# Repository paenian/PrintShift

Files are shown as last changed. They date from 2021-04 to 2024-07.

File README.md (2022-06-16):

# Prusa Mini Conveyor Belt!

Status: Fully Functional!

Quick overview - this repo contains all the files I used to add a conveyor belt to my Prusa Mini.

The latest version fits a Prusa Mini, and lives here: https://github.com/paenian/PrintShift/tree/main/prusa%20mini/printshift%204.0%20ejector

## BELT MATERIAL
The current belt is made from .2mm thick Kapton, ordered from AliExpress and lasercut.  You can totally hand-cut it, but tracking of the belt is a bit of a pain.

The belt is designed to be easily replaced - other materials I have used:
 * .01" polyester film: Cuts easily, prints stick very well with hairspray.  This belt has higher thermal expansion, but with PLA or lower temps on the heater it works great, and is quite cheap.  It does break down at PETG temperatures, so I recommend the kapton as the most versatile belt.
   * https://www.mcmaster.com/8567K92/
   * Use hairspray to help prints stick.
 * .225mm Kapton: Low thermal expansion.  More expensive than the polyester.
   * https://www.aliexpress.com/item/4000699107361.html?spm=a2g0s.9042311.0.0.19534c4dqCLd9z
   * Use hairspray to help prints stick.
 * .005" ULTEM/PEI film: Prints stick well, but it's too flexible.  After ~10 hours printing, sheet sheared while printing.  It was under a lot of tension.  Gets expensive quick.
   * https://catalog.cshyde.com/item/films/ultem-pei-polyethermide-resin/36-5f
 * .01" ULTEM/PEI film: Same story as the .005; less flexible, of course, so prints warped less on it.  However, it did shear mid-print after maybe 100 hours of printing - it lasted longer, but split right in two.  My assumption is more due to fatigue from all the rolling.
   * https://catalog.cshyde.com/item/films/ultem-pei-polyethermide-resin/36-10f

 I have used thicker and stiffer belts, too - various stainless steels and conveyor materials, usually covering the belt itself in PET tape to get good adhesion and release.  However, these require larger, stronger rollers - so aren't compatible with the printers in this repository.

## CONTROL
The belt is controlled by a microswitch mounted on the top of the Z axis.  When the Z gets high enough and Y is forward enough, your parts scoot.  The nice part is no modification of the firmware is required - just some special start and end GCODE in your slicer.  I do take power for the motor from inside the Prusa Mini box for neatness - I like my printers as self-contained as possible.

The other modifications to the Prusa Mini involve raising the bed 4mm - so combined with the switch up top, you're losing about 15mm of usable Z axis.

Right now, the belt is 145mm in width - so your Y axis shrinks a bit when printing on the belt.  You can, however, still print using the entire bed - just put the metal build plate on top of the belt!

## INSTALLATION
The projects in this repository are best described on YouTube: https://www.youtube.com/paulchase

Instructions, videos, tips and tricks will all be posted there.

This project is supported by patrons on Patreon - go to https://www.patreon.com/PrintShift if you'd like to help develop part ejecting printers!

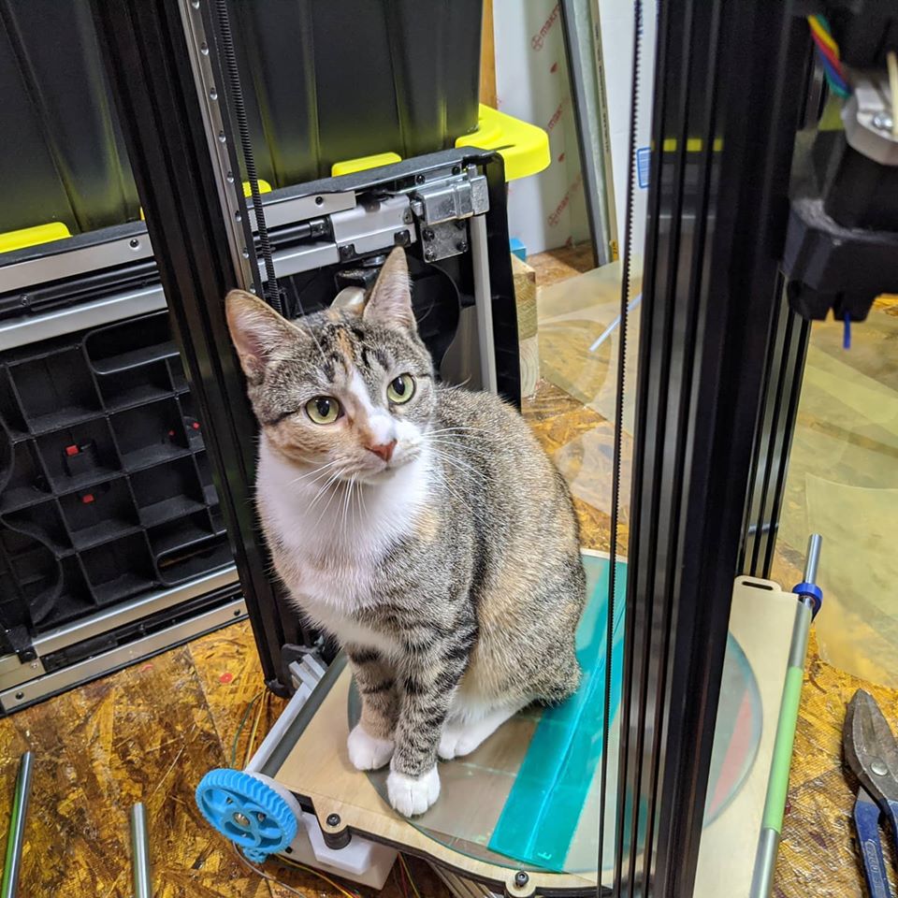
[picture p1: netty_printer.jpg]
Netty is the official mascot


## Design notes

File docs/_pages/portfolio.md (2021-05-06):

---
title: PrintShift Guides
layout: collection
permalink: /portfolio/
collection: portfolio
entries_layout: grid
classes: wide
---

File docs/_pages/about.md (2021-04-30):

---
permalink: /about/
title: "About"
---

The PrintShift Project is adding conveyor belts to conventional 3D printers.  The project began by adding part ejection to Prusa Minis, which is now feature-complete and has been running for thousands of printing hours.

The project will continue to work on belts, part ejection and related technologies, as well as working to improve the Prusa Mini's ejector.

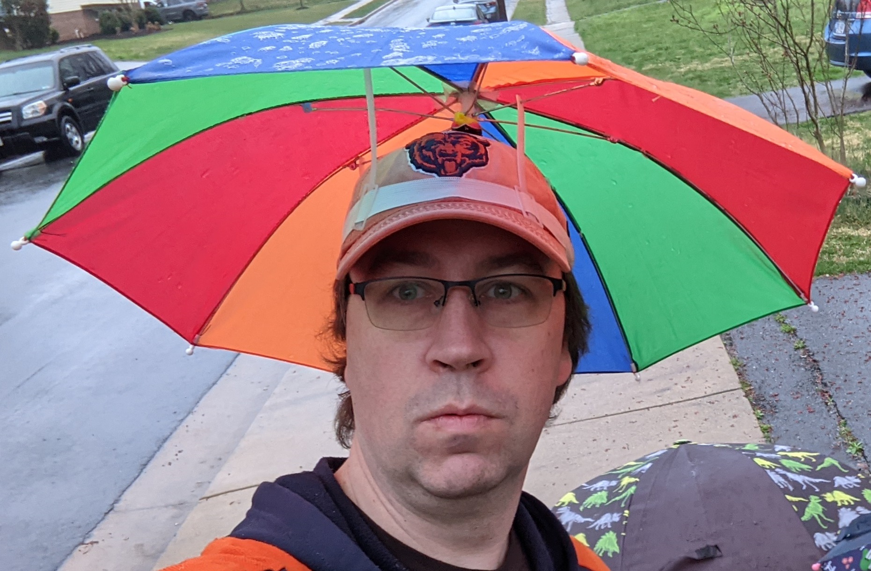
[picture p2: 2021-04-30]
docs/assets/images/bio-photo.jpg

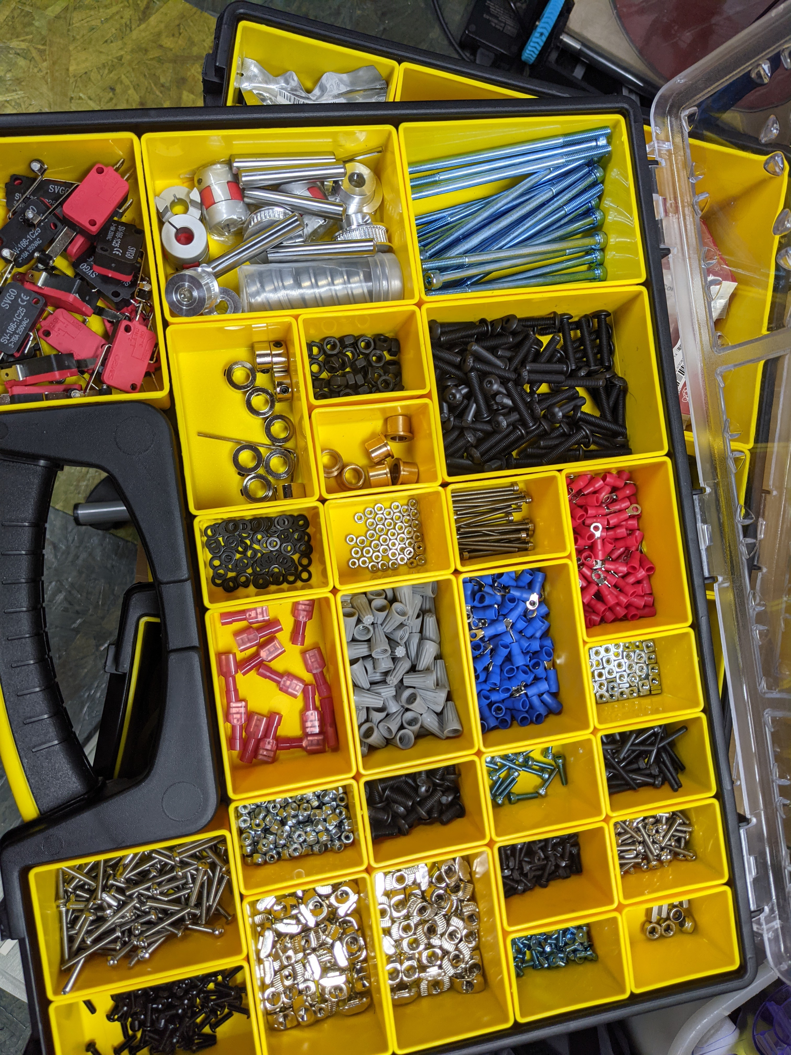
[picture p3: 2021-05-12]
docs/assets/images/BoM-photo.jpg

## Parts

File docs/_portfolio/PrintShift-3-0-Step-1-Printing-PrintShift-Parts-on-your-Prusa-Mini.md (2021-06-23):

---
title: "PrintShift 3.0 Step 1: Printing PrintShift Parts on your Prusa Mini"
---

# PrintShift 3.0 Build Series: Step 1

This page details how to print the PrintShift parts.  I like to print the parts on the Prusa Mini that's destined to be PrintShift-ed - that way you know the machine is up and running and ready to go.  If your mini's acting up or failing in any way... repair it before you upgrade it!

## Materials Needed
1. Prusa Mini.  Yeah.  The whole thing.
   * Prusa sells 'em mostly built: [Prusa Mini+](https://shop.prusa3d.com/en/3d-printers/994-original-prusa-mini.html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)
   * Or barely assembled: [Prusa Mini+ Kit](https://shop.prusa3d.com/en/3d-printers/1387-original-prusa-mini-kit.html)
   * The mostly built goes together in under an hour; kit is maybe ten hours of building.
2. Filament!
   * You need some high-temperature filament like ABS, PETG, ASA or better for the bed-touching components.
   * You need some stiff filament for the Motor Mount and Standoff - PLA is fine, pretty much anything except TPU.

## Tools Needed
1. The Prusa Mini includes all the tools that you'll need for this portion of the build :-)
   * I do generally use my own 2.5mm allen wrench
   * And some side cutters to trim the zip tie

## Procedure
1. Build your Prusa Mini!  Just follow Prusa's instructions
  * Mostly Built:  [Prusa Mini+ Build Instructions](https://help.prusa3d.com/en/guide/building-your-mini_177717)
  * Kit: [Prusa Mini+ KIT Build Instructions](https://help.prusa3d.com/en/category/original-prusa-mini-kit-assembly_1215)
2. Test Print!  Prusa includes a few on the USB stick that comes with the printer.
3. Print Large PrintShift Parts
  * These are printed with .25mm layers, 3 perimeters, 50% cubic infill.  They need to be strong and rigid.
  * [Rear Motor Plate](https://github.com/paenian/PrintShift/blob/main/prusa%20mini/printshift%203.0%20ejector/rear%20motor%20plate.stl)
  * [Motor Plate Standoff with Pi](https://github.com/paenian/PrintShift/blob/main/prusa%20mini/printshift%203.0%20ejector/motor%20plate%20standoff%20-%20with%20pi.stl)

4. Print PrintShift - all small parts
  * This is all of the other parts; they need to handle the higher temperatures of the bed, so must be ABS, ASA, PETG or similar. 
  * Mine are printed in blue ABS, .25mm layers, 3 perimeters, 50% cubic infill.  They need to be strong, rigid, and stable up to 100C.
  * [Small Parts](https://github.com/paenian/PrintShift/blob/main/prusa%20mini/printshift%203.0%20ejector/PrintShift%20-%20all%20small%20parts.stl)
5. Print (optional) Raspberry Pi components
  * [pi 4 case top](https://github.com/paenian/PrintShift/blob/main/prusa%20mini/mini%20mounts%20and%20enhancements/raspi/Pi_4_Case_40mm_fan_top%20v3.stl)
  * [pi 4 case bottom](https://github.com/paenian/PrintShift/blob/main/prusa%20mini/mini%20mounts%20and%20enhancements/raspi/Pi_4_Case_bottom%20v3.stl)
  * [pi 3 case top](https://github.com/paenian/PrintShift/blob/main/prusa%20mini/mini%20mounts%20and%20enhancements/raspi/pi_3_case_top.stl)
  * [pi 3 case bottom](https://github.com/paenian/PrintShift/blob/main/prusa%20mini/mini%20mounts%20and%20enhancements/raspi/pi_3_case_bottom.stl)
  * [Rear camera mount](https://github.com/paenian/PrintShift/blob/main/prusa%20mini/mini%20mounts%20and%20enhancements/raspi/rear%20camera%20mount.stl)
6. Gather the rest of the parts from the [Bill of Materials](/portfolio/Bill-of-Materials/) and start [Building the Belt](/portfolio/PrintShift-3-0-Step-2-Belted-Bed-Build)!

## Video Walkthrough
{% include video id="aPgevA5sr5U" provider="youtube" %}

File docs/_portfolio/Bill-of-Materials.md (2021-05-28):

---
title: "PrintShift Bill of Materials"
excerpt: "Shortcut to the Google Docs active BOM, with some discussion on parts."
header:
  image: /assets/images/BoM-photo.jpg
  teaser: assets/images/BoM-photo.jpg
---
# PrintShift Bill of Materials

The LIVE Bill of Materials will live here:

[BoM on Google Sheets](https://docs.google.com/spreadsheets/d/1gTF6RvdNjgoJNNBqXj-OhuOjt69_Wzujfkq8HkN1fU4/edit?usp=sharing)
Anyone can comment on the google doc - ideally, comments will be resolved and then removed.

[CSV Snapshot as of 5/11/2021](/assets/PrintShift BOM - Sheet1.csv)

## BoM Sections
The BoM is divided into sections based on where the parts are used; this is to try to help organize it, and to more easily edit and update.  

### Conveyor Belt Hardware
There is a separate page to cover and discuss [belt materials](/portfolio/Belt Materials/)

The rest of the parts here are hardware for mounting the belt to the Prusa Mini's bed carriage.  The conveyor belt hardware can be added at any point, and while it raises the bed 4mm it does not affect normal operation of the mini in any way... at least until you slide a belt onto it :-)

Basically none of these parts can be substituted out without redesigning something, but there are bound to be cheaper suppliers, especially in quantity.

### Ejector Hardware
These parts are everything required to mount and run the ejector motor, as well as connect it to the conveyor belt mounted on the bed.
This includes the control microswitch and wiring.

Generally, installing these I would include the 5v buck converter to run a raspberry pi - although using wire nuts to attach means it's easy to add later.

A lot of these parts (wire nuts, crimp lugs, getting power for the motor in the first place) could be substituted out as desired; I chose them as the easiest to install reliably.

### Belt Material
The Kapton and various tapes used for the belt.  I treat tapes as '1 roll per printer' so they add a little more to the BoM than I would like... but it's better to be expansive I think.

### Raspberry Pi
Mounting a Raspberry Pi and running Octoprint on the mini is optional, but adds a huge amount of functionality.  In the future, Prusa has said that they would expand the capabilities of the BuddyBoard and its ethernet port, so perhaps the pi will become redundant... but I don't think that it will.

The Raspberry Pi + camera allows you to access your printer from far away to monitor and start or queue prints.  Additionally, I use Octoprint plugins to connect my machines to the cloud and add print queueing.

### Optional Parts
This includes parts trays, GoPro mounts, my silly clock mount (I love it), and the base to put the printer on if you utilize a rackmount or other print farm system.

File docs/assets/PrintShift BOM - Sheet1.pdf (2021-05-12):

# of PrintShifts to build | 10 Part | Type | Notes | Quantity Needed Per-Machine Price | Pack Quantity | Pack Price | Price Per Part | Packs Needed | extra part quantityPurchase Price | Purchase Link Conveyor Belt Hardware Shaft collar | 8mm | For front of drive roller | 1 | $0.90 | 10 | $8.99 | $0.90 | 1 | 0 | $8.99 | https://smile.amazon.com/gp/product/B07V41FRZS/ref=ppx_yo_dt_b_asin_title_o00_s01?ie=UTF8&psc=1

8mm shaft, 210mm | hardened steel | drive roller - cut into 183mm for the idler, remainder works great for the drive roller 1 | $7.20 | 2 | $14.39 | $7.20 | 5 | 0 | $71.95 | https://smile.amazon.com/Linear-Motion-FEYRINX-Hardened-Printer/dp/B085DQYQYH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
8mm shaft, 183mm | hardened steel | idler - cut down from the 400mm above | 0 | $0.00 | 2 | $14.39 | $7.20 | 0 | 0 | $0.00
flanged bushings | 8mm | drive roller guides | 2 | $6.88 | 1 | $3.44 | $3.44 | 20 | 0 | $68.80 | https://www.mcmaster.com/5448T2/ M3 Hex Standoffs, 10mm long 4.5 or 5mm hex | lift the bed up | 6 | $6.30 | 1 | $1.05 | $1.05 | 60 | 0 | $63.00 | https://www.mcmaster.com/94868A166/ M3 screw, 8mm | flat head | replace the bed screws - easier to deal with9 | $1.64 | 50 | $9.10 | $0.18 | 2 | 10 | $18.20 | https://www.mcmaster.com/91304A101/ M5 screws, 25mm | button head | tension the idler | 2 | $0.31 | 50 | $7.86 | $0.16 | 1 | 30 | $7.86 | https://www.mcmaster.com/91306A669/ M5 nuts | hex | tension the idler | 2 | $0.04 | 100 | $1.76 | $0.02 | 1 | 80 | $1.76 | https://www.mcmaster.com/90592A095/
Ejector Hardware F608ZZ flanged ball bearings | 8x22x7 | 2 | $2.74 | 10 | $13.69 | $1.37 | 2 | 0 | $27.38 | https://smile.amazon.com/gp/product/B07N62N7N2/ref=ppx_yo_dt_b_asin_title_o00_s00?ie=UTF8&psc=1
flexible shaft coupling | 8mm to 8mm | Link the belt and the motor | 1 | $6.50 | 2 | $12.99 | $6.50 | 5 | 0 | $64.95 | https://smile.amazon.com/gp/product/B08QVKMDC6/ref=ppx_yo_dt_b_asin_title_o00_s01?ie=UTF8&psc=1
40T GT2 pulley | 8mm bore | Attach to belt | 1 | $4.00 | 2 | $7.99 | $4.00 | 5 | 0 | $39.95 | https://smile.amazon.com/gp/product/B07K6BRL4K/ref=ppx_yo_dt_b_asin_title_o00_s01?ie=UTF8&psc=1
20T GT2 pulley | 6mm bore | Attach to motor | 1 | $1.60 | 5 | $7.99 | $1.60 | 2 | 0 | $15.98 | https://smile.amazon.com/gp/product/B08P6KY773/ref=ppx_yo_dt_b_asin_title_o08_s00?ie=UTF8&psc=1 GT2 continuous belt | 79 teeth | connect the pulleys | 1 | $1.19 | 10 | $11.88 | $1.19 | 1 | 0 | $11.88 | https://smile.amazon.com/gp/product/B014QKEH26/ref=ppx_yo_dt_b_asin_title_o07_s00?ie=UTF8&psc=1
24v motor | 20RPM | ejector motor | 1 | $13.99 | 1 | $13.99 | $13.99 | 10 | 0 | $139.90 | https://smile.amazon.com/gp/product/B08FBBXZ67/ref=ppx_yo_dt_b_search_asin_title?ie=UTF8&psc=1
8mm dowel pin | 40mm long | ejector drive shaft | 1 | $0.96 | 10 | $9.60 | $0.96 | 1 | 0 | $9.60 | https://www.mcmaster.com/91595A573/ M3 screws, 12mm | socket head | Mount the motor | 2 | $0.10 | 100 | $5.19 | $0.05 | 1 | 80 | $5.19 | https://www.mcmaster.com/91292A114/ M5 screws, 100mm | socket head | Rear standoff for the motor assembly | 2 | $1.53 | 10 | $7.66 | $0.77 | 2 | 0 | $15.32 | https://www.mcmaster.com/91502A159/ M3 screws, 30mm | socket head | mount the switch | 2 | $0.42 | 50 | $10.51 | $0.21 | 1 | 30 | $10.51 | https://www.mcmaster.com/91290A130/ 3030 T-Nuts, M3 | post-assembly | mount the switch | 2 | $0.46 | 50 | $11.57 | $0.23 | 1 | 30 | $11.57 | https://smile.amazon.com/gp/product/B07GVJFZV8/ref=ppx_yo_dt_b_search_asin_title?ie=UTF8&psc=1 SV-166-1C25 microswitch | long hinge roller | ejector activator | 1 | $0.55 | 20 | $10.99 | $0.55 | 1 | 10 | $10.99 | https://smile.amazon.com/SV-166-1C25-Industrial-Switches-Terminals-Momentary/dp/B087PLT9MD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 Ring Terminal | M3, 22-16AWG wirepower the ejector | 1 | $0.07 | 150 | $9.99 | $0.07 | 1 | 140 | $9.99 | https://smile.amazon.com/smseace-Insulated-Electrical-Connectors-Assortment/dp/B08B5VS8ZR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 Spade connectors | 22-16AWG | wire in the switch | 2 | $0.50 | 80 | $19.98 | $0.25 | 1 | 60 | $19.98 | https://smile.amazon.com/gp/product/B07GP96LSS/ref=ppx_yo_dt_b_search_asin_image?ie=UTF8&psc=1 Wire Nuts | gray, 2*22awg terminals wire up the switch | 2 | $0.04 | 1000 | $17.99 | $0.02 | 1 | 980 | $17.99 | https://smile.amazon.com/Maxxima-Electrical-Connector-Screw-Terminal/dp/B07ZP8K8GJ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
22awg wire | Need about 2 meters total wire it all up | 0.5 | $1.41 | 6 | $16.95 | $2.83 | 1 | 1 | $16.95 | https://smile.amazon.com/gp/product/B07T4SYVYG/ref=ppx_yo_dt_b_search_asin_title?ie=UTF8&psc=1

Belt Material
.225mm Polyamide Film (Kapton).225x520x1m | The belt is 155mm wide by 430mm long - so cut 155mm strips, then trim down. | You can get 6 belts per mm, but quantity here is 2 - you always want a spare belt handy. 2 | $8.14 | 6 | $24.41 | $4.07 | 4 | 4 | $97.64 | https://www.aliexpress.com/item/4000473438004.html?spm=a2g0s.9042311.0.0.41374c4dFBWN0U
Powdercoating Tape | polyester film + silicone adhesive, .001" thick, 2" wide | 1 | $11.98 | 1 | $11.98 | $11.98 | 10 | 0 | $119.80 | https://www.mcmaster.com/7630A796/ Kapton Tape | 2" wide, Polyimide film + silicone adhesive, .0025" thick | 1 | $15.97 | 1 | $15.97 | $15.97 | 10 | 0 | $159.70 | https://smile.amazon.com/Heat-Resistant-Tape-Sublimation-Temperature/dp/B07KXXT1Y9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 Painter's Tape | 2" wide | 1 | $4.79 | 6 | $28.75 | $4.79 | 2 | 2 | $57.50 | https://smile.amazon.com/ScotchBlue-2090-48A-CP-Painters-Polypropylene-Backing/dp/B000A3DQGW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
Raspberry Pi Parts Buck Converter Module | USB-C | power the Raspberry Pi | 1 | $14.99 | 1 | $14.99 | $14.99 | 10 | 0 | $149.90 | https://smile.amazon.com/gp/product/B07ZQB6S3L/ref=ppx_yo_dt_b_asin_title_o05_s00?ie=UTF8&psc=1 USB->MicroUSB cable | 1ft | connect pi to the prusa mini | 1 | $7.99 | 1 | $7.99 | $7.99 | 10 | 0 | $79.90 | https://smile.amazon.com/gp/product/B07PFZDQP6/ref=ppx_yo_dt_b_asin_title_o05_s00?ie=UTF8&psc=1 Pi Camera Cable | 30cm | connect up pi camera | 1 | $1.33 | 6 | $7.99 | $1.33 | 2 | 2 | $15.98 | https://smile.amazon.com/gp/product/B08WLQBB93/ref=ppx_yo_dt_b_asin_title_o04_s00?ie=UTF8&th=1 Arducam | cheaper Pi Camera | 1 | $9.99 | 1 | $9.99 | $9.99 | 10 | 0 | $99.90 | https://smile.amazon.com/gp/product/B012V1HEP4/ref=ppx_yo_dt_b_asin_title_o04_s00?ie=UTF8&psc=1 Raspberry Pi 4 | 2GB | No need for more ram, but I think the faster processor is worth it over the older Pis. 1 | $34.99 | 1 | $34.99 | $34.99 | 10 | 0 | $349.90 | https://www.microcenter.com/product/621439/raspberry-pi-4-model-b-2gb-ddr4
2.5mm screws, 35mm long | socket head | 3 | $1.44 | 25 | $12.03 | $0.48 | 2 | 20 | $24.06 | https://www.mcmaster.com/91292A313/ 2.5mm nuts | hex | 3 | $0.22 | 50 | $3.69 | $0.07 | 1 | 20 | $3.69 | https://www.mcmaster.com/94150A310/
Optional Parts Collection Tray | 1 | $2.66 | 3 | $7.99 | $2.66 | 4 | 2 | $31.96 | https://smile.amazon.com/gp/product/B086X2YM9Q/ref=ppx_yo_dt_b_asin_title_o05_s01?ie=UTF8&psc=1
TOTAL PRICE | Per Machine, perfect: | $173.81 | $1,858.62 Per Machine, in quantity: | $185.86 Total for | 10 | $1,858.62
Price without Pi or Optional Parts | Per Machine, perfect: | $100.19 Per Machine, in quantity: | $110.33 Total for | 10 | $1,103.33

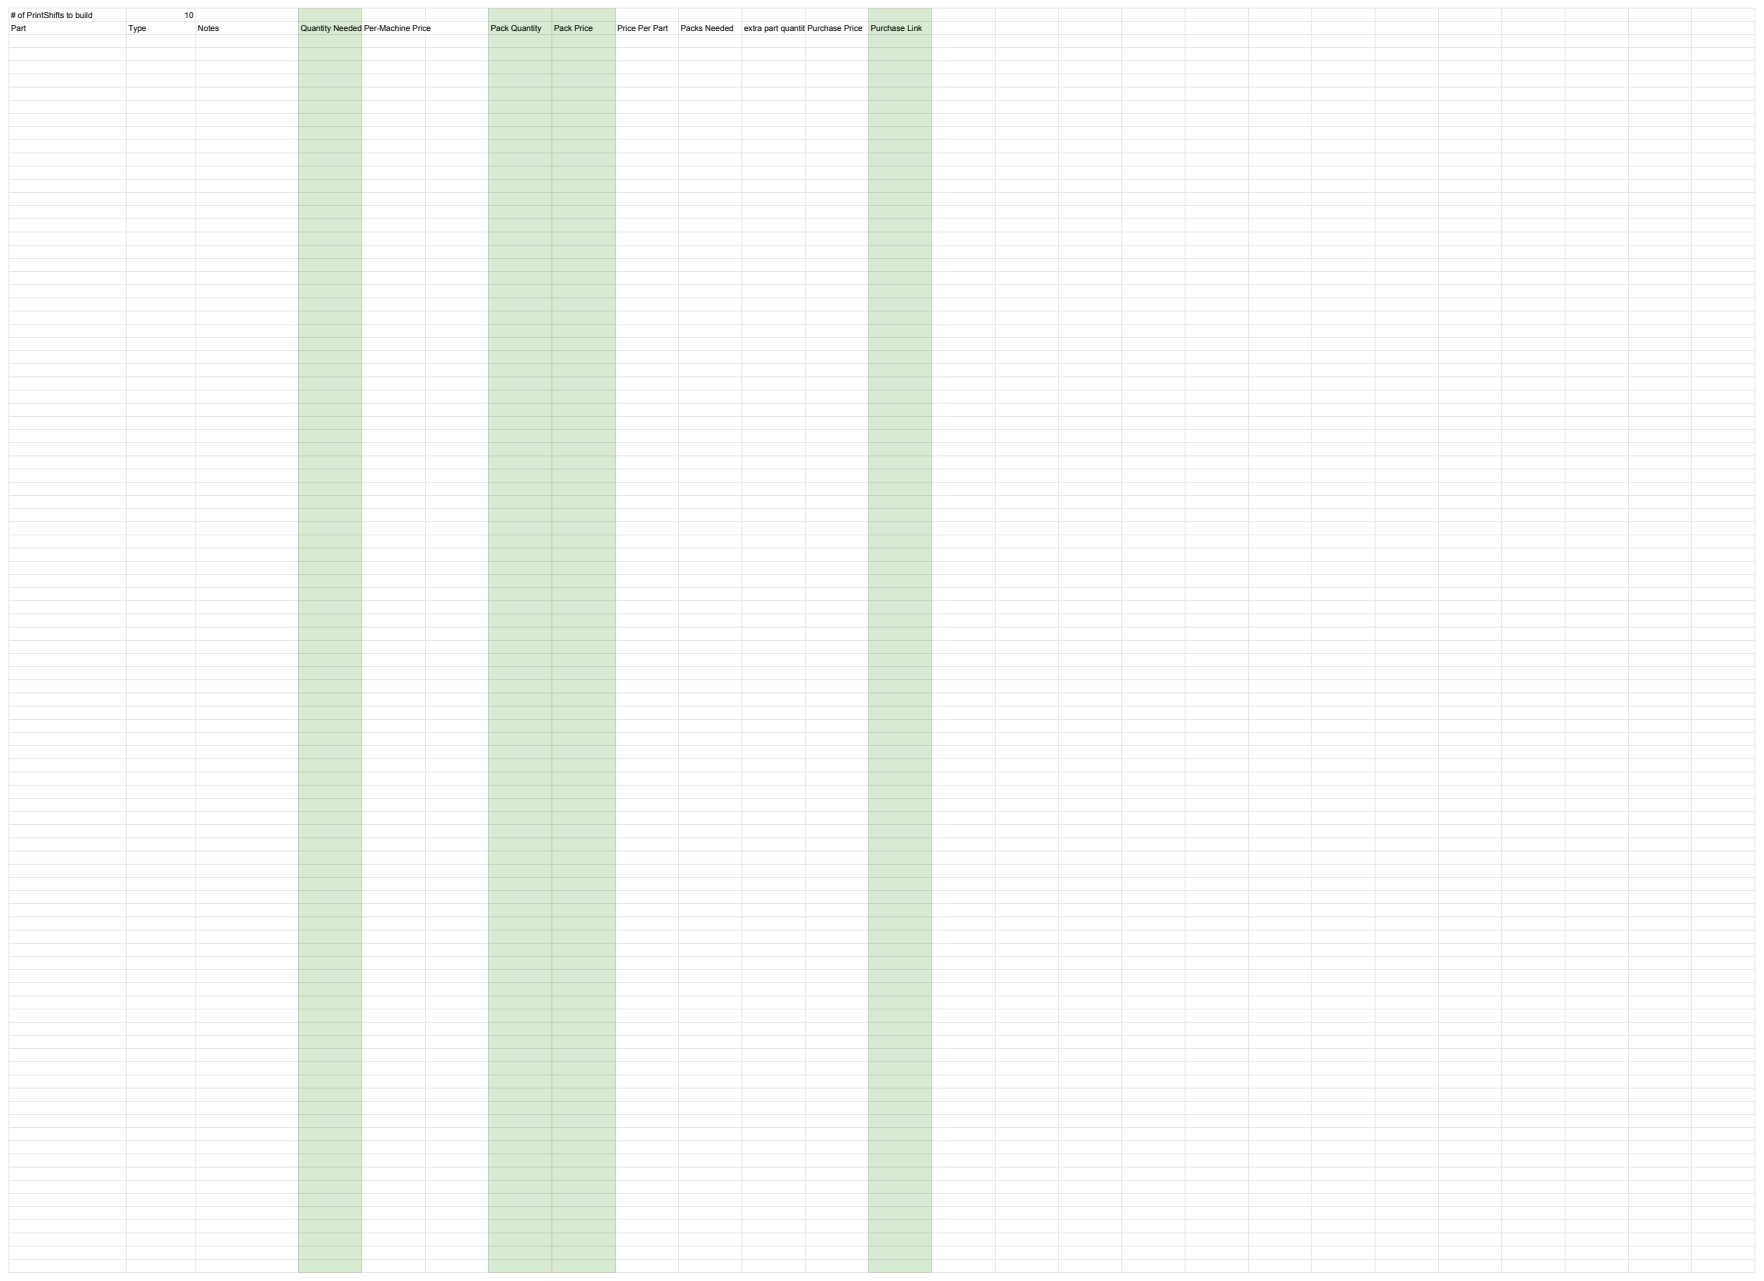
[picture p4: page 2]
# of PrintShifts to build; 10 Part; Type; Notes; Quantity Needed Per-Machine Price; Pack Quantity; Pack Price; Price Per Part; Packs Needed; extra part quantityPurchase Price; Purchase Link

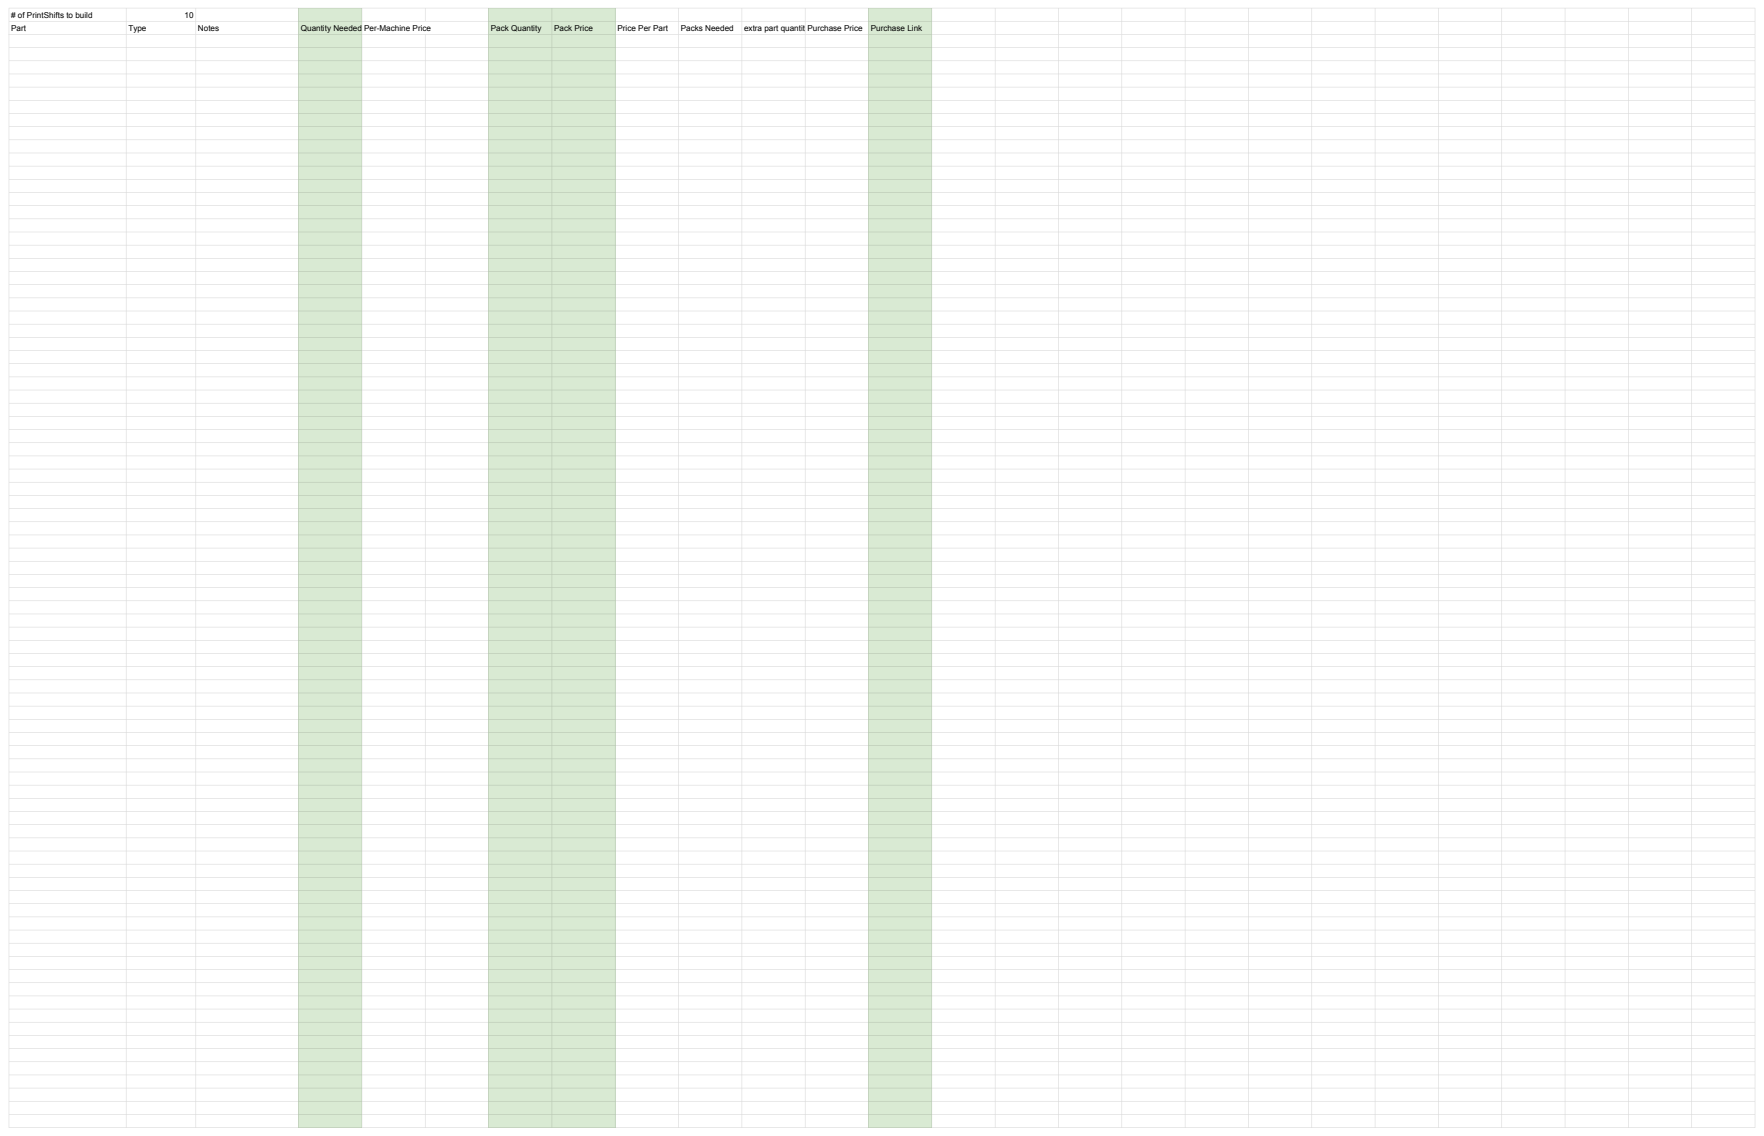
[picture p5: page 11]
# of PrintShifts to build; 10 Part; Type; Notes; Quantity Needed Per-Machine Price; Pack Quantity; Pack Price; Price Per Part; Packs Needed; extra part quantityPurchase Price; Purchase Link

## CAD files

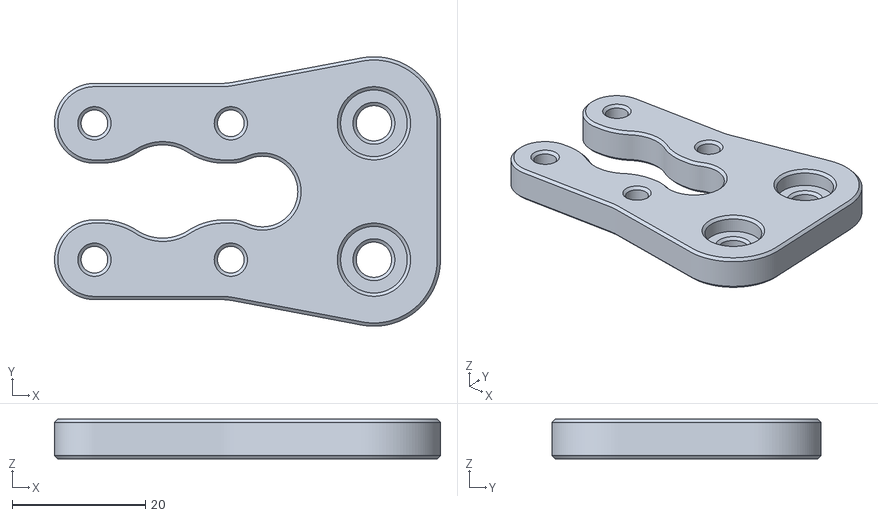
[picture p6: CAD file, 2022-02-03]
large bed ejector/doppelbot mounts/smooth rod mount.stl
58.0 x 40.5 x 6.00

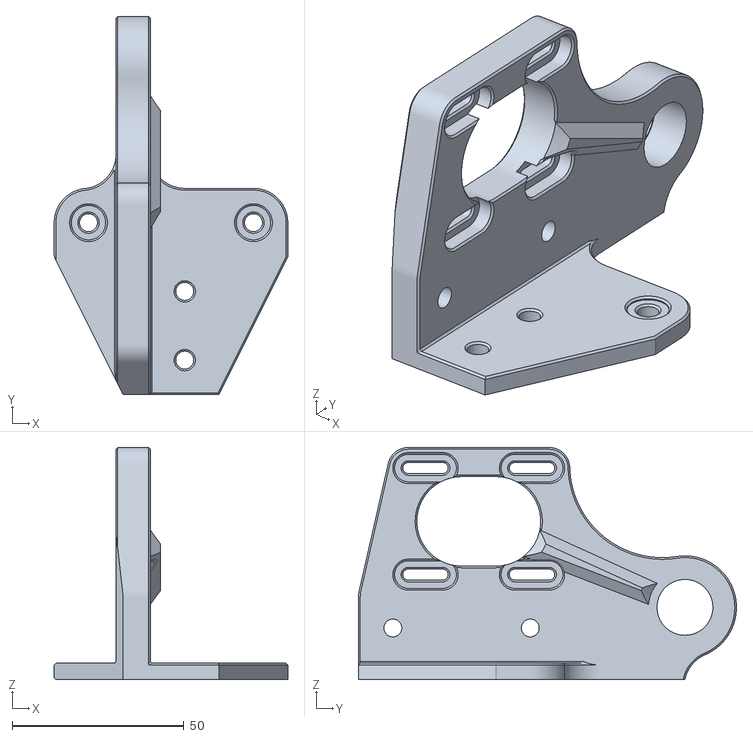
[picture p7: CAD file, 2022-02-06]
large bed ejector/motor and drive roller mount.stl
68.0 x 110.0 x 67.5

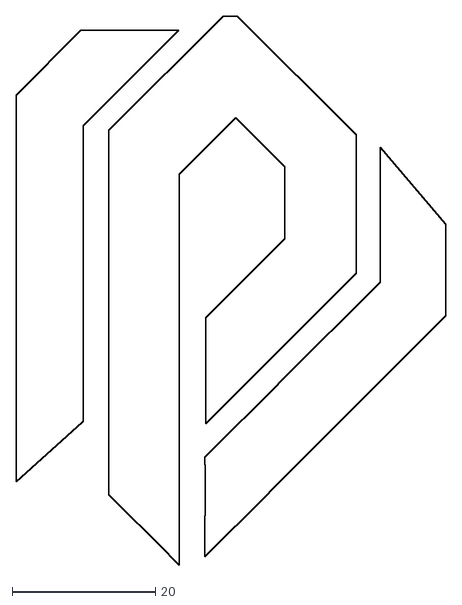
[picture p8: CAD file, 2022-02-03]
PrintShift logos/printshift_logo.dxf
60.0 x 76.6

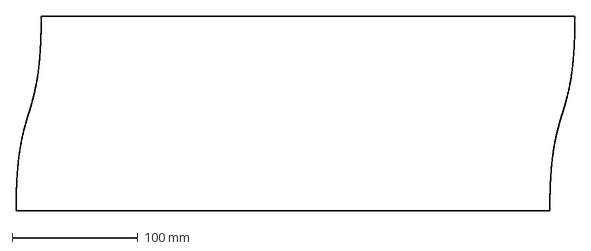
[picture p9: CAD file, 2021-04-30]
prusa mini/bed lasercutting/flat_angle-425x155.dxf
445.0 x 155.0 mm

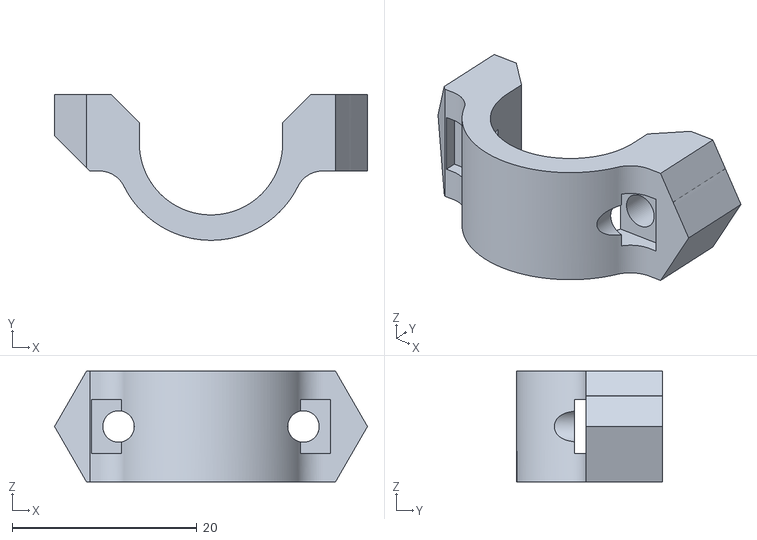
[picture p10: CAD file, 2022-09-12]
prusa mini/mini mounts and enhancements/prusa mini lm8uu clamp.stl
33.9 x 15.8 x 12.0

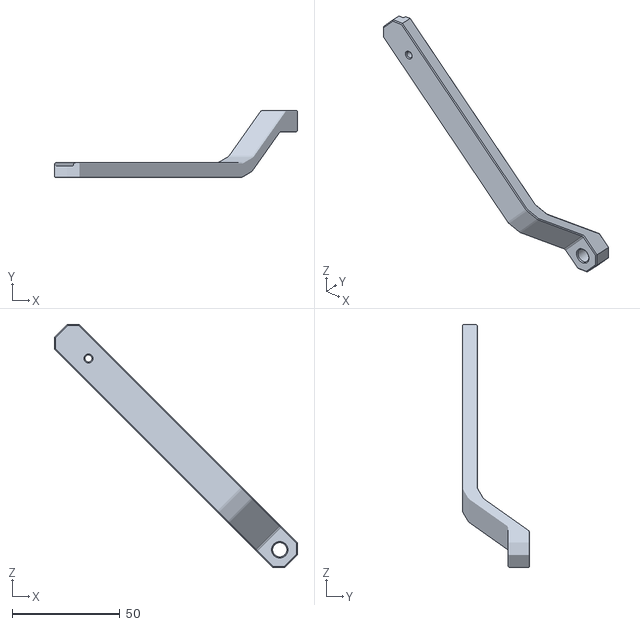
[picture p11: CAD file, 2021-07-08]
prusa mini/mini mounts and enhancements/raspi/corner webcam mount.stl
112.8 x 31.2 x 112.8

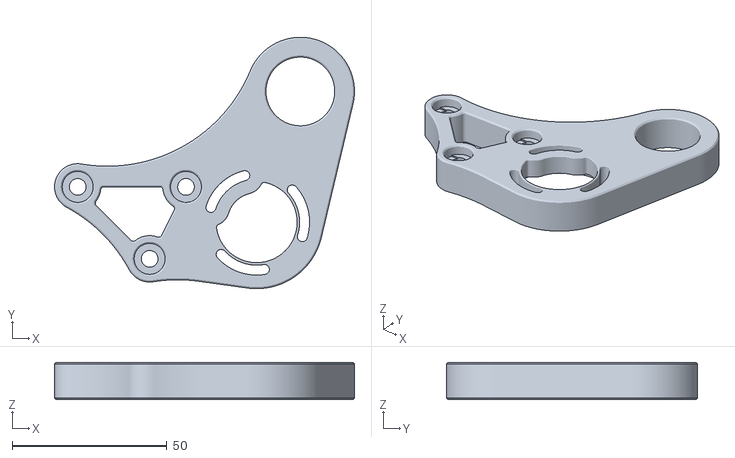
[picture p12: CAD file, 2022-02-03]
prusa mini/printshift 3.0 ejector/rear motor plate updated.stl
96.9 x 81.2 x 12.0

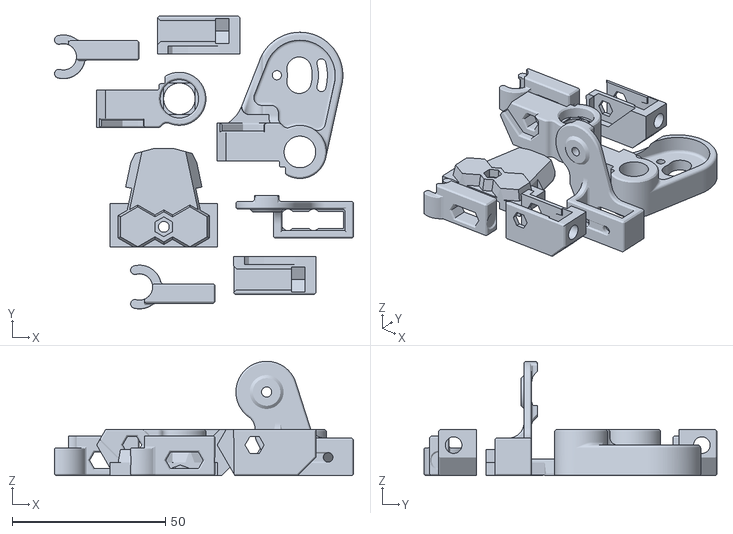
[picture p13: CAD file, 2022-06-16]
prusa mini/printshift 4.0 ejector/all parts arranged.stl
97.4 x 95.4 x 37.3

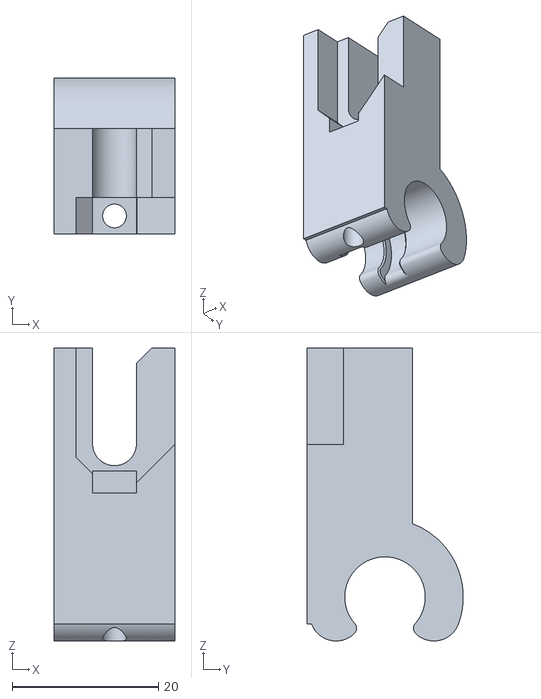
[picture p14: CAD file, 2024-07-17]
prusa mini/printshift 5.0 ejector/tensioner rod mount right.stl
16.5 x 21.4 x 40.1

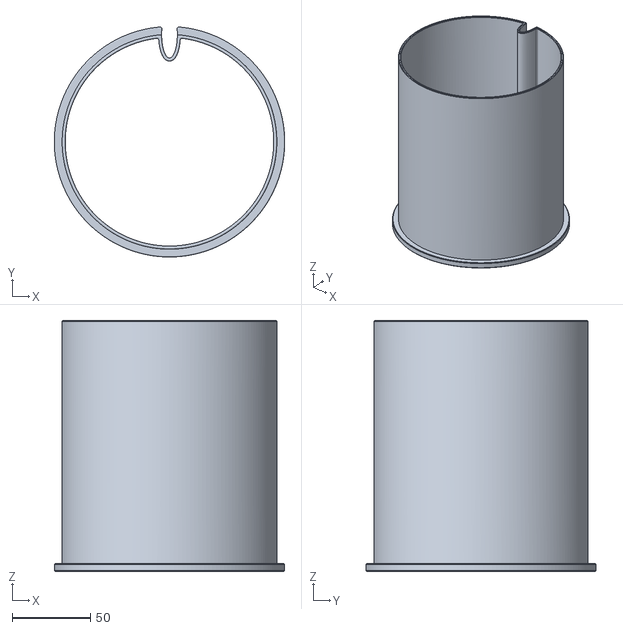
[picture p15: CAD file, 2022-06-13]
prusa mini/Prusa Mini Belt Jig.stl
146.9 x 146.6 x 160.0

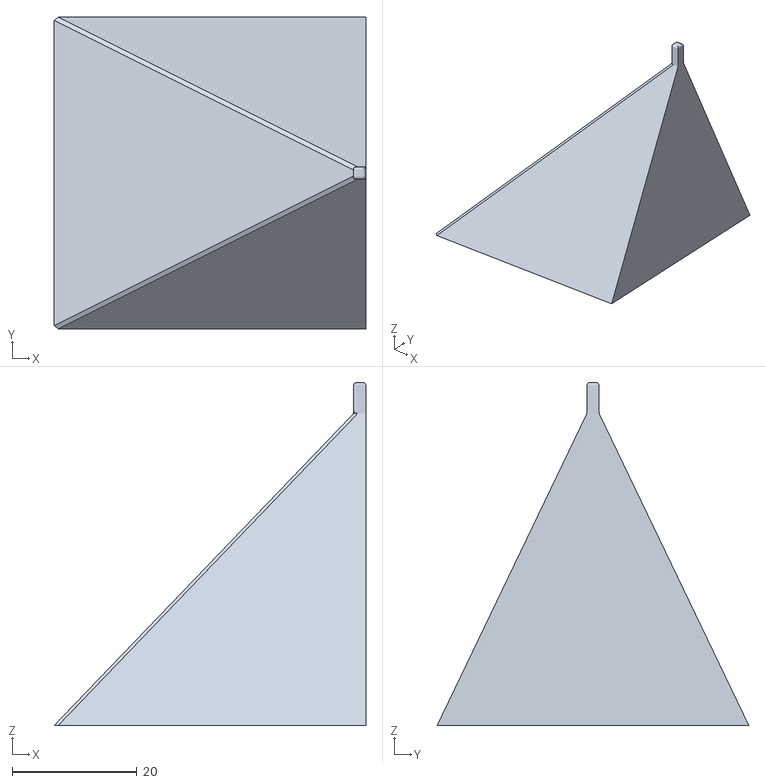
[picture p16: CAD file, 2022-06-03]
Test Objects/side pull tester.stl
50.0 x 50.0 x 55.0

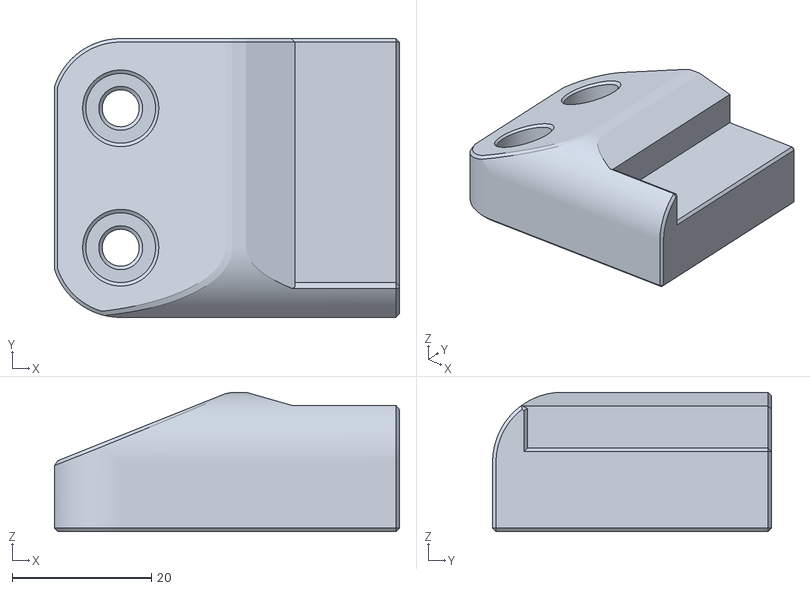
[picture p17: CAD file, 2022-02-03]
large bed ejector/doppelbot mounts/bed corner.stl
49.5 x 40.0 x 20.0

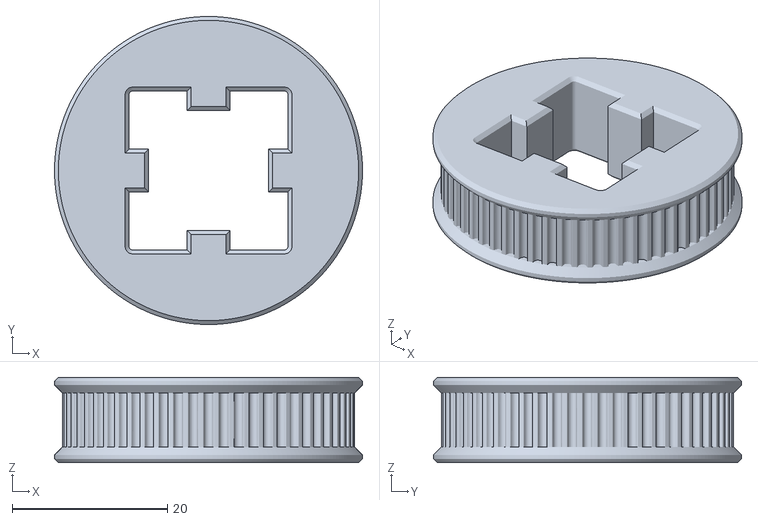
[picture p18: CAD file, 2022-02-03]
large bed ejector/drive pulley.stl
39.7 x 39.7 x 11.0

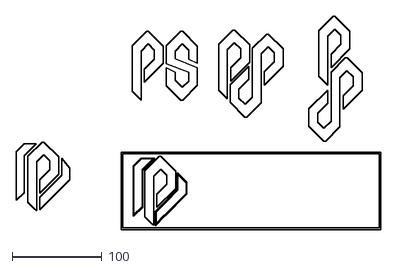
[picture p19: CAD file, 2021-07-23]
PrintShift logos/printshift.dxf
405.9 x 237.1

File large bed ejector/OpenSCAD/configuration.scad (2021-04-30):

in = 25.4;

screw_slop = .2;
slop = .2;
laser_slop = -.1;

beam = 20;

//standard screw variables
m3_nut_rad = 6.01/2+slop;
m3_nut_height = 2.4;
m3_rad = 3.1/2+slop;
m3_cap_rad = 3.5;
m3_cap_height = 2;
m3_sq_nut_rad = 7.9/2;

m4_nut_rad = 7.66/2+slop;
m4_nut_height = 3.2;
m4_rad = 4/2+slop;
m4_cap_rad = 7/2+slop;
m4_cap_height = 2.5;

m5_nut_rad = 8.79/2;
m5_sq_nut_rad = (8*sqrt(2)+slop/2)/2;
m5_nut_rad_laser = 8.79/2-.445;
m5_nut_height = 4.7;
m5_rad = 5/2+slop;
m5_rad_laser = 5/2-.1;
m5_cap_rad = 10/2+slop;
m5_cap_height = 3;
m5_washer_rad = 11/2+slop;

ten24_rad = (.19*in/2+slop);
ten24_cap_rad = (.361*in/2+slop);
ten24_cap_height = .101*in+slop;
ten24_nut_rad = ((3/8*in)*cos(180/6))/2;
ten24_sq_nut_rad = ((3/8*in)*sqrt(2))/2+slop/2;

ten24_nut_height = 1/8*in+slop;

ten24_rad_laser = ten24_rad+laser_slop/2;
ten24_sq_nut_rad_laser = ten24_sq_nut_rad+laser_slop/2;
ten24_sq_nut_flat = 9.5;
ten24_sq_nut_flat_laser = ten24_sq_nut_flat+laser_slop;

//makes all the holes have lots of segments
$fs=.5;
$fa=.1;

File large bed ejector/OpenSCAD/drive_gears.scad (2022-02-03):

include <configuration.scad>
use <herringbone_gears.scad>
use <functions.scad>

//gear variables

motor_shaft_rad = 5/2+.2;
//drive_shaft_rad = 12/2+.2;

drive_shaft_rad = 25.4/2/2+.2;

small_teeth = 9;
big_teeth = 47;
gear_thick = 13;
distance_between_axles = 50;

circular_pitch = 360*distance_between_axles/(small_teeth+big_teeth);

part = 101;

if(part == 1){
   mirror([0,0,1]) motor_drive_gear();
}

if(part == 2){
    mirror([0,0,1]) roller_drive_gear();
}

if(part == 3){
    mirror([0,0,1]) roller_drive_gear(solid = true);
}

if(part == 100){
    assembled();
}

if(part == 101){
    assembled(solid = true);
}

module assembled(solid = false){
    difference(){
        union(){
            mirror([0,0,1]) motor_drive_gear();
            mirror([0,0,1]) roller_drive_gear(solid = solid);
        }
        //translate([0,100,0]) cube([200,200,200], center=true);
    }
}

module motor_drive_gear(){
    translate([distance_between_axles+1,0,0]) gear1(gear1_teeth = small_teeth, circular_pitch=circular_pitch, gear_height=gear_thick);
}

module roller_drive_gear(wall = 3, solid = false){
    %motor_drive_gear();
    
    radius = gear_radius(big_teeth, circular_pitch);
    outer_radius = gear_outer_radius(big_teeth, circular_pitch);
    
    gear_chamfer_radius = (outer_radius - radius) / tan(45);
    
    lift = gear_thick+1;
    
    difference(){
        union(){
            //gear
            chamfered_herring_gear(height=gear_thick, number_of_teeth=big_teeth, circular_pitch=circular_pitch, teeth_twist=-1);
        }
        
        if(solid == false){
        //the shaft
        translate([0,0,-.5]) cylinder(r=drive_shaft_rad, h=gear_thick+1);
        
        //gotta hold it on somehow
        
                //screws and nuts to mount to the shaft
                translate([0,0,gear_thick/2]) for(i=[0:120:359]) rotate([0,0,i]) {
                    rotate([90,0,0]) cap_cylinder(r=m5_rad, h=25);
                    rotate([90,0,0]) cap_cylinder(r=m3_rad+.25, h=75);
                    //nut trap
                    rotate([90,0,0]) cylinder(r2=8.135/cos(180/6)/2,r1=8.135/cos(180/6)/2+.3, h=10, $fn=6);
                }
                
        translate([0,0,gear_thick/2]) difference(){
            //hollow most of the gear
            cylinder(r=outer_radius-6.1, h=gear_thick+1, center=true);
            
            //but leave the middle for attachments
            difference(){
                cylinder(r=drive_shaft_rad+7, h=gear_thick+2, center=true);
            }
            
            //biohazard!
            for(i=[30:120:359]) rotate([0,0,i]) difference(){
                translate([(outer_radius-3.5)/2,0,0]) cylinder(r=(outer_radius-5)/2,h=gear_thick, center=true);
                translate([(outer_radius-4+8-2.5)/2,0,0]) cylinder(r=(outer_radius-5-8)/2,h=gear_thick+1, center=true);
            }
        }
    }}
}

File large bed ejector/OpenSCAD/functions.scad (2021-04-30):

include <configuration.scad>

slot_w = 6;
slot_d = 6;
slot_inner_w = 14;
slot_inner_h = 4;

module beam_2060(height=20, v=false, slop=0){
    translate([-beam,0,0]) beam(height=height, v=v, slop=slop);
    beam(height=height, v=v, slop=slop);
    translate([beam,0,0]) beam(height=height, v=v, slop=slop);
}

module beam_2040(height=20, v=false, slop=0){
    translate([-beam/2,0,0]) beam(height=height, v=v, slop=slop);
    translate([beam/2,0,0]) beam(height=height, v=v, slop=slop);
}

module beam(height=20, v=false, slop=0){
	rad = 2;
	

	center_w = 5;

	difference(){
		hull(){
			for(i=[0:90:359])
				rotate([0,0,i])
					translate([beam/2-rad, beam/2-rad, 0]) cylinder(r=rad+slop, h=height);
		}

		//slots
		beamSlots(height=height, v=v, slop=0);

		//center hole
		cube([center_w, center_w, height*3],center=true);
	}
}

module beamSlots(height=20, v=false, slop=0){
    for(i=[0:90:359]) rotate([0,0,i]){
        translate([beam/2,0,0]) cube([slot_d*2-slop*2,slot_w-slop*2,height*3],center=true);
        //v rail
        if(v==true){
            hull(){
                translate([beam/2-slot_d+slot_inner_h+slop,0,0]) cube([.1,slot_w-slop*2,height*3],center=true);
                translate([beam/2-slot_d+slot_inner_h+10-slop,0,0]) cube([.1,slot_w+20-slop*2,height*3],center=true);
            }
        }
    }
    nutSlots(height=height, slop=slop);
}

module nutSlots(height=20, slop=0){
    //angled inner
    for(i=[0:90:359]) rotate([0,0,i]){
			hull(){
				translate([beam/2-slot_d+slop,0,0]) cube([.1,slot_w-slop*2,height*3],center=true);
				translate([beam/2-slot_d+slot_inner_h-slop,0,0]) cube([.1,slot_inner_w-slop*4,height*3],center=true);
			}
        }
}

module endScrew(height=20){
    cylinder(r=m5_rad, h=height*3, center=true);
}

module beamHoles(height=20, slop=.25){
    nutSlots(height=height, slop=slop);
    endScrew(height=height);
}

//a cylinder with a flat on top - for drawing vertical holes.
module cap_cylinder(r=1, h=1, center=false){
	render() union(){
		cylinder(r=r, h=h, center=center);
		intersection(){
			rotate([0,0,22.5]) cylinder(r=r/cos(180/8), h=h, $fn=8, center=center);
			translate([0,-r/cos(180/4),0]) rotate([0,0,0]) cylinder(r=r/cos(180/4), h=h, $fn=4, center=center);
		}
	}
}

//holes for the motor
module motor_holes(screw_rad = m3_rad+slop/2, screw_w = motor_screw_sep, slot=2, slide = false, height = wall*3){
    bump_rad = 12;
    
    cylinder(r=bump_rad, h=height, center=true);
    %translate([0,0,-20]) cylinder(r=pulley_flange_rad, h=height*2);
    if(slide == false){
        for(i=[0:90:359]) rotate([0,0,i]) translate([screw_w/2, screw_w/2, 0]){
            hull(){
                translate([-slot/2,-slot/2,0]) cylinder(r=screw_rad, h=height, center=true);
                translate([slot/2,slot/2,0]) cylinder(r=screw_rad, h=height, center=true);
            }
        }
    }else{
        for(i=[0:1]) for(j=[0:1]) mirror([i,0,0])mirror([0,j,0]) translate([screw_w/2, screw_w/2, 0]){
            hull(){
                translate([0,-slot/2,0]) cylinder(r=screw_rad, h=height, center=true);
                translate([0,slot/2,0]) cylinder(r=screw_rad, h=height, center=true);
            }
        }
    }
}

module motor_body(extra = .1, thick=wall){
    intersection(){
        hull() for(i=[0:1]) for(j=[0:1]) mirror([i,0,0]) mirror([0,j,0]) translate([motor_w/2, motor_w/2, 0]) 
            cylinder(r=extra, h=thick, center=true);
        cylinder(r=motor_r+extra, h=thick, center=true);
    }
}

module screw_hole_m3(cap=false, onion=0, height=wall){
    screw_hole(cap=cap, onion=onion, cap_height=m3_cap_height, rad=m3_rad, cap_rad=m3_cap_rad, height=height);
}

module nut_hole_m3(cap=false, onion=0, height=wall){
    nut_hole(cap=cap, onion=onion, nut_height=m3_nut_height+1, rad=m3_rad, nut_rad=m3_nut_rad, height=height);
}

module screw_hole_m4(cap=false, onion=0, height=wall){
    screw_hole(cap=cap, onion=onion, cap_height=m4_cap_height, rad=m4_rad, cap_rad=m4_cap_rad, height=height);
}

module screw_hole_m5(cap=false, onion=0, height=wall){
    screw_hole(cap=cap, onion=onion, cap_height=m5_cap_height, rad=m5_rad, cap_rad=m5_cap_rad, height=height);
}

//nuthole with a nice recess for the cap.
module nut_hole(cap=false, onion=0, height=wall){
    translate([0,0,-nut_height-1])
        if(cap==true){
            cap_cylinder(r=rad, h=height*3);
        }else{
            cylinder(r=rad, h=height*3);
        }
	translate([0,0,0])
        cylinder(r1=nut_rad, r2=nut_rad+slop, h=height, $fn=6);
        
}

//nuthole with a nice recess for the cap.
module screw_hole(cap=false, onion=0, height=wall){
    translate([0,0,cap_height-.05+onion])
        if(cap==true){
            cap_cylinder(r=rad, h=height);
        }else{
            cylinder(r=rad, h=height);
        }
	translate([0,0,cap_height-height])
        if(cap==true){
            cap_cylinder(r=cap_rad, h=height);
        }else{
            cylinder(r=cap_rad, h=height);
        }
}

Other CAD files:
prusa mini/bed lasercutting/rounded_notch-425x155.dxf
prusa mini/mini mounts and enhancements/Orbiter_2.0_Prusa_Mini.stl
prusa mini/mini mounts and enhancements/raspi/pi_3_case_top.stl
prusa mini/printshift 3.0 ejector/lifted belt shaft mount - fixed 10mm sleeve bushing.stl
large bed ejector/OpenSCAD/herringbone_gears.scad
Test Objects/Belt Deflection Tester.stl
Test Objects/test sled.stl
large bed ejector/100mm roller.stl
large bed ejector/doppelbot mounts/inner bed corner.stl
large bed ejector/doppelbot mounts/leadscrew mount.stl
large bed ejector/doppelbot mounts/new_hotend_mount.stl
large bed ejector/doppelbot mounts/rail bed corner.stl
large bed ejector/drive_pulley.stl
large bed ejector/straight roller.stl
large bed ejector/tensioner corner.stl
large bed ejector/trapezoid roller.stl
prusa mini/PrintShift Belt Jig v2.f3d
prusa mini/bed lasercutting/chevron-425x155.dxf
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

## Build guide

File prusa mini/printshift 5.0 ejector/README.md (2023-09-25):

# PrintShift 5.0

5th generation Prusa Mini part ejection system.

## Status: Experimental IN WORK

These parts are in use, but could all use some refinement.

## BoM

### Lift the bed up
 - 6 Hex Standoffs - female threaded 5mm or 4.5mm hex standoff 10mm long.  Source: https://www.mcmaster.com/94868A166/
 - 6 flat head screws - M3 by 8mm long, yes you could re-use Prusa's original ones but they're short and torx, which annoys me.  Source: https://www.mcmaster.com/91304A101/

### Drive Roller and Idler Mounting
 - 4 bearings - MR148-2RS Deep Groove Ball Bearings 8mm Inner Dia 14mm OD 4mm thick
 - 2 8mm by 200mm long hardened steel shafts.
 - 1 ~160mm EPDM rubber sleeve - 5/16 or 8mm in diameter, wall thickness 1/16" or 1.5mm or less.  Source: https://www.mcmaster.com/9776T15/
   - This provides grip to drive the belt.  1mm adhesive EPDM foam sheet works, too, but it's a pain to apply it smoothly.

### Clutch
 - 1 8mm Needle Roller Bearing, One Way Clutch 8mm Bore 14mm OD 12mm Width

### Tension the Belt
 - 2 M3 square nuts
 - 2 M3 screws, 15mm long

### The Belt itself!
 - .2mm thick Kapton film
   - 155mm wide, 430mm long. Source: https://www.aliexpress.com/item/2255800287123252.html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
   - 1 meter of film should get you 6 belts 
   - There's a jig for making these in the Prusa Mini directory
 - super thin PET tape.  Source: https://www.mcmaster.com/7630A175/
   - This is the best tape I've found.  It still tends to get damaged when printed on, so I time the motor to do a single revolution and don't print on the seam.
 - NEW: magnetic stainless steel shim stock, 6" wide: https://www.mcmaster.com/9500K101/

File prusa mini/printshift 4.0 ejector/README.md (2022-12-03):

# PrintShift 4.0

4th generation Prusa Mini part ejection system.

## Printing the Parts
There's an [all parts arranged.stl](https://github.com/paenian/PrintShift/blob/main/prusa%20mini/printshift%204.0%20ejector/all%20parts%20arranged.stl) with each part laid out and oriented for printing.  No supports are necessary.  PLA works OK, higher-temperature plastics make me less nervous about the ones that touch the bed.
Each part is listed below, so you don't have to guess its name.

## BoM
These are all the parts needed to build PrintShift 4.0.  Feel free to ping me with alternate sources, especially for non-US places.
I've got the 4.0 BOM in Google Sheets here, as well:
https://docs.google.com/spreadsheets/d/1Y6tmWdhaA39aywXKX1IuBWYhULWI4l2Ml0a-xL-PMI8/edit#gid=0

### Lift the bed up
 - 6 Hex Standoffs - female threaded 5mm or 4.5mm hex standoff 10mm long.  Source: https://www.mcmaster.com/94868A166/
 - 6 flat head screws - M3 by 8mm long, yes you could re-use Prusa's original ones but they're short and torx, which annoys me.  Source: https://www.mcmaster.com/91304A101/
##### Printed Parts
 - [MINI-heatbed-cable-cover-bottom.stl](https://github.com/paenian/PrintShift/blob/main/prusa%20mini/printshift%204.0%20ejector/MINI-heatbed-cable-cover-bottom.stl)
   - We need to replace the original heatbed cable cover - shortening it to make room for the tensioner.

### Motor and Idler Mounting
 - 1 Motor - 488:1 6v 20D Metal Gear Motor - Source: https://www.pololu.com/product/3711
   - To fit the other parts, the motor needs a 4mm shaft and two M2.5 screws spaced 7.5mm from the shaft.
   - Another motor is fine, but you'd need to adjust other parts, too.   
 - 2 Motor Mounting Screws - M2.5 by 10mm flat head screws - Source: https://www.mcmaster.com/92125A088/
 - 4 bearings - 8mmx12mmx3.5mm - that's 8mm inside diameter, 12mm outside diameter and 3.5mm thick.  Source: https://smile.amazon.com/gp/product/B082PPLHLQ/ref=ppx_yo_dt_b_search_asin_title?ie=UTF8&psc=1
 - 1 4mm bore 16 tooth Gt2 pulley.  Source: https://smile.amazon.com/gp/product/B09N79R6TG/ref=ppx_yo_dt_b_search_asin_title?ie=UTF8&psc=1
 - 1 8mm bore 40 tooth Gt2 pulley.  Source: https://smile.amazon.com/gp/product/B07K6BRL4K/ref=ppx_yo_dt_b_search_asin_title?ie=UTF8&psc=1
 - 1 110-2GT closed-loop Gt2 belt - 6mm wide, 55 teeth.  Source: https://smile.amazon.com/BEMONOC-2GT-Timing-Belt-110-2GT-6/dp/B014SSZ3EM
 - 2 8mm by 200mm long hardened steel shafts.  Source: https://smile.amazon.com/dp/B08HYJRRXD/
   - The drive shaft is a tiny bit short doing it like this, but the belt locks it in place so I figure it's fine.
 - 1 ~160mm EPDM rubber sleeve - 5/16 or 8mm in diameter, wall thickness 1/16" or 1.5mm or less.  Source: https://www.mcmaster.com/9776T15/
   - This provides grip to drive the belt.  1mm adhesive EPDM foam sheet works, too, but it's a pain to apply it smoothly.
##### Printed Parts
 - [direct mount motor lifted bushing.stl](https://github.com/paenian/PrintShift/blob/main/prusa%20mini/printshift%204.0%20ejector/direct%20mount%20motor%20lifted%20bushing.stl)
   - holds the motor, and the rear of the drive shaft
 - [direct mount idler lifted bushing.stl](https://github.com/paenian/PrintShift/blob/main/prusa%20mini/printshift%204.0%20ejector/direct%20mount%20idler%20lifted%20bushing.stl)
   - holds the front of the drive shaft

 ### Tension the Belt
 - 2 M5 hex nuts - really any will do - https://www.mcmaster.com/90592A095/
 - 2 M5 screws - I use 20mm long button head M5 screws, but if you have some other M5 lying around they're fine.  Source: https://www.mcmaster.com/97763A458/
 ##### Printed Parts
 - [tensioner body.stl](https://github.com/paenian/PrintShift/blob/main/prusa%20mini/printshift%204.0%20ejector/tensioner%20body.stl)
   - You need two: one normal, one mirrored.
 - [tensioner rod holder bearing.stl](https://github.com/paenian/PrintShift/blob/main/prusa%20mini/printshift%204.0%20ejector/tensioner%20rod%20holder%20bearing.stl)
   - You need two: one normal, one mirrored.

 ### Microswitch ACTIVATE!
 - Microswitch - 10T85U - 5amp, 250v, roller-lever.  Source: https://smile.amazon.com/MXRS-SPDT1NO-Momentary-Roller-Switch/dp/B07MW3W79B/
 - Wire - 20awg wire, I like the silicone cuz it's super flexible.  Source: https://smile.amazon.com/dp/B08CC1DLQF
 - HeatShrink Tubes - red solder seal wire connectors.  Source: https://smile.amazon.com/gp/product/B07N2G71C2
   - You can also solder the connections
 - M3 30mm T-nut - post-insert.  Source: https://smile.amazon.com/Assembly-Nickel-Plated-Fastener-Aluminum-Profile/dp/B07GVJFZV8
   - These can also be printed: https://www.printables.com/model/127404-3030-m3-drop-in-t-nut-remix
   - if you print them, you need an M3 nut also.
 - M3 by 10mm screw.  Source: https://www.mcmaster.com/91290A115/
 ##### Printed Parts
 - [limit switch mount.stl](https://github.com/paenian/PrintShift/blob/main/prusa%20mini/printshift%204.0%20ejector/limit%20switch%20mount.stl)
   - You need two: one normal, one mirrored.

 ### The Belt itself!
 - .2mm thick Kapton film
   - 155mm wide, 430mm long. Source: https://www.aliexpress.com/item/2255800287123252.html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
   - 1 meter of film should get you 6 belts 
   - There's a jig for making these in the Prusa Mini directory
 - super thin PET tape.  Source: https://www.mcmaster.com/7630A175/
   - This is the best tape I've found.  It still tends to get damaged when printed on, so I time the motor to do a single revolution and don't print on the seam.

 ### POWER.
There are two options for power: external, or steal from the Mini.  Either way, we need 5v at a fair bit of amperage to power the ejection motor and the (optional, but super useful) Raspberry Pi.
External means you don't need to open up your mini's electronics bay, but then your printer takes up two wall plugs.
Internal makes your printer a bit more portable, but functionally it'll work exactly the same.

 #### External
 - 5v, 6A DC Power Supply.  This one can handle 120 or 240 volts.  Source: https://smile.amazon.com/dp/B08762BC1K
   - this plugs into the wall.  Hide it with your printer's big old brick power supply.
 #### Internal
 - 12v/24v in 5V out DC-DC power converter, 10A.  6 amps would be fine if you can find one.  Source: https://smile.amazon.com/dp/B01M03288J
   - This would need to plug into the Prusa Mini's power supply, generally inside the electronics enclosure.

 #### Adding a Pi
 It's just nice to plug 'em in properly, I don't feel comfy feeding power in through the GPIO pins.
 - Pi 4: 
   - USB-C male plug, 10".  Source: https://smile.amazon.com/dp/B09C7SLHFP
 - Pi 3 and before:
   - USB-Micro-B plug, 12".  Source: https://smile.amazon.com/Micro-Cable-12inch-22AWG-Pigtail/dp/B09DKYPCXK

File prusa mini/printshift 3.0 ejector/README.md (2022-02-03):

#  Prusa Mini Conveyor Belt!

Status: Fully Functional!

This directory is the latest PrintShift Prusa Mini repository.

There are two rear motor plates - one of our users found that the updated dimensions fit his modern Prusa Mini.
Eventually I'll get another and verify, but for now - if the official doesn't fit, and the updated does - please let me know!

Thanks!

Netty is the official mascot

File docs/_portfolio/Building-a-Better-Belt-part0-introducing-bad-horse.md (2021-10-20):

---
title: "Making a Better Belt - Who is Bad Horse?"
---

# ok, what's this Bad Horse that I've never heard about?

I started developing PrintShift on Prusa Minis in order to make it more accessible - but I started my research on beltprinters well before PrintShift became a thing.  Here I'll give a brief overview of development, and 

## Early Days
The first part-ejector was developed by a makerbot user, Charles Edward Pax, and his 2010 blog about it is [still online](https://charlespax.wordpress.com/2010/03/17/makerbot-conveyor-belt/) - yeah.  This was further developed by Charles as a Makerbot employee, and unfortunately patented - which is one reason why later development shifted towards angled printers.
[The first part ejected on video!](https://www.youtube.com/watch?v=J-I98wzJUJo)

## Angled Printers?  What?
Angled printers are ones where one of the axes is not perpendicular to the other two.  This can also be used to enable infinitely long prints, or at least prints that are longer than the printer.  The first of these was a project by Bill Steel and unveiled in 2017 at the [MidwestRepRapFestival](https://hackaday.com/2017/03/25/mrrf-17-the-infinite-build-volume-printer/) - to the surprise of everyone.
A Kickstarter for [Blackbelt3D](https://blackbelt-3d.com/) came a few months later, followed by a growing set of similar machines.
Just to list a few, I've got my [Printrbelt](https://www.youtube.com/watch?v=CK171ShYIeA) here, there's also the [White Knight](https://www.youtube.com/channel/UCai5w5hngu5sUbCGnCuKQYA) which contributed to [Creality's CR-30](https://www.creality3dofficial.com/products/cr-30-infinite-z-belt-3d-printer) and the [Powerbelt3D](https://powerbelt3d.com/) printers - which are cool because you can buy 'em.

I did design my own, scaled-up Printrbelt, which was where I started to play with different conveyor belts.  However, it's pretty oversized, which means that changing the belt could get expensive for more exotic materials.

## Bertha
This is when the pandemic hit my shop... which left me with free time, some odd parts and a powerful need to print face shields.  So I built two more belt-based part ejection machines.
Bertha is my deltabot, or rather Berthest, apparently.  I've been messing with and modifying deltabots for a while; its [part ejector](https://www.youtube.com/watch?v=_Ud6TqBTL1Y) is based on some new ideas I had that I'll cover at the end.  Of note is that this is a cartesian part ejector - the nozzle is perpendicular to the build plate.  Another note is that this printer has two Y axes - the weird combo axis from the Deltabot, and the bed itself - powered by stepper motors, it can be moved precisely.

Thomas Sanladerer captured my reasoning for moving away from angled-bed 3D Printers in his [lowered CR-30 video](https://www.youtube.com/watch?v=tP1g2b8RmYE&t=4s), and again with his 
[real print bed](https://www.youtube.com/watch?v=8O9E9rcH6Us) automated voron.

## Bad Horse
So, bad horse.  Bad Horse was designed as a development printer to test out new conveyor belt ideas, and that's what I plan to use it for again going forwards.
It was built from parts I had on hand, and I solved problems as they came up.  The unique feature of this printer is that its normal Y axis is on a gantry - so while it's shaped like a Prusa style bedslinger, the bed is in fact fixed in place.

Or, I could fix the gantry in place - and use the bed to supply all Y movement - because this belt is driven by stepper motors.
OR - and this is why you want a cartesian part ejector - I can use all four motion axes and print on an angled plane of my choosing.  So Bad Horse could be a pure part-ejecting printer, a lowered CR-30, or even print on a 30 degree plane to make parts longer than the printer.  The best part about this method is that it can live entirely in the slicer - no modifications to the printer at all.

First, though, I'd like to use it to test out some new conveyor belts, and I'd also like to get RepRapFirmware running on this machine - I've spent a bit too much time lying to Marlin about the bed being another extruder, and trying to add the bed as a dependent axis... it's better to keep the firmware stock and do the coordinate manipulation in the slicer or a post-processor.  If anyone wants to help write that, let me know - and as always happy printing.

## Video Walkthrough
{% include video id="_wT68gNBn74" provider="youtube" %}

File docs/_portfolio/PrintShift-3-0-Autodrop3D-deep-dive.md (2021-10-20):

---
title: "PrintShift 3.0: Cloud Deep Dive: Autodrop3d"
---

# Autodrop3d Deep Dive

## Materials Needed
1. Prusa Mini, assembled, printing, with the conveyor belt bed, ejector motor, controls, and the [Raspberry Pi](https://www.raspberrypi.org) attached and loaded up with Octoprint.  Yeah.
2. Electrons

## Tools Needed
 * A computer to pester your [Octoprint](https://octoprint.org) install with
 * The Internet

## Cloud Services
One way to get more out of your part-ejecting 3D Printer is to put it on the CLOUD.  The benefit of a cloud service is that it puts your 3D Printer online, so that you can monitor it remotely and even start prints.  There are, of course, other ways to do this like tunneling through your router, but the cloud takes care of security and configuration headaches.

## Installing and Taming AutoDrop3d
Here I'll be talking about the use and installation of [Autodrop 3d](https://www.autodrop3d.com/) - doing a deep dive on this particular cloud printing service.  Autodrop 3D is the only part-ejection-aware cloud service that I am -aware- of.  It's a bit rough around the edges, but I'm hoping that calling attention to it - getting it more users - that's where y'all come in - will help speed up the improvement of the service.  Right now, it's free for personal use and offers printers the ability to charge for external prints on their machine - more on that later.

It can be installed on its own, as an Octoprint replacement or as an octoprint plugin; personally, I like the plugin approach as the most flexible, but it is a little more involved.  They also sell a pi with Autodrop pre-installed, and even sell part-ejecting Kossel machines with a cool pusher ejector - worth checking out, certainly.

The goal of this printer is to open it up to test prints - from anywhere in the world.  I've also be fired up a streaming option, so that you can share your creation as its being printed - I'm expecting folks to use it to send messages, or other silly things.

Anyways.  Before installing the Autodrop3d plugin, you need Python 3 - which you have if you're on Octopi 0.18.  If you're not:
1. Take a backup from inside OctoPrint's 'Backup and Restore' tab, and download it.
2. Download & install OctoPi 0.18
3. Once installed, you can restore your backup using 'Backup and Restore' again.

### Installing the Plugin
The [github](https://github.com/Autodrop3d/AD3d-octoprint-connect/archive/master.zip) repo has the latest; last I checked the plugin doesn't appear in the Octoprint plugin repository.

### Setting up Autodrop3d
Material, location, printer, etc - it's a bit of a boondoggle.  I'm not going to run through all of it, just an overview, and thankfully once it's set up you generally don't need to mess with it.

### Safe slicing settings for Autodrop3d
We're going to add a raft and supports for every part - to ensure build plate adhesion.  Additionally, this raft is beefier than most!  Generally, I'm using PrintShift to print large batches of the same part - so tuning the gcode for each part is essential to get the best prints you know, in order to sell parts.  This internal slicer is designed to be used by non-experts printing one-off random parts - so we're being conservative.

### Watch your print being printed!
So, when you want to print, you can upload a new part or - check this out - it's got three 3D editors BUILT IN.
 * A mesh editor/sculptor, that's, well, pretty hard to use to make things, but can be used to smooth out an existing STL or something.  I'm not familiar with these at all, though, so can't compare it to something like Z-Brush.
 * OpenSCAD!  Yeah.  Pretty bare bones, but, it's in there
 * JSketcher, a Javascript-only parametric modeler.
These are nice, but, well, for most jobs if I'm on the internet already I'd be using tinkercad or OnShape.
So mostly I just upload STLs.

I'll have CannonFodder here streaming the prints live - and will make weekly roundups of interesting streams from the machine up on this channel.

## Congratulations!
With this step, you've got a fully functional part-ejecting 3D Printer that can be controlled from anywhere in the world - and by anyone if you're not careful!  Happy printing, as always.

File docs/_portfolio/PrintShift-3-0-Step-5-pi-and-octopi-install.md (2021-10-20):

---
title: "PrintShift 3.0 Step 5: Raspberry Pi and Octopi Install"
---

# PrintShift 3.0 Build Series: Step 5

Once you've got your Prusa Mini able to eject parts, we highly recommend adding a Raspberry Pi to it and running Octoprint.  This allows you to access your printer remotely, and with plugins you can also print continuously, or even hook the machine up for random users to use.  More on that next time - for now just focus on the mechanics.

### Previous Step:
[PrintShift Gcode: Ejecting Parts](/portfolio/PrintShift-3-0-Step-4.5-PrintShift-Gcode)
### Next Step:
[PrintShift Step 6: Too Much Automation](/portfolio/PrintShift-3-0-Step-6-cloud-automation)

## Materials Needed
1. Prusa Mini, assembled, printing, with the conveyor belt bed, ejector motor, and control microswitch attached and wired together.
2. Pi Case - the top and bottom of either the Pi 3 or Pi 4 case.
   * [pi 4 top](https://github.com/paenian/PrintShift/blob/main/prusa%20mini/mini%20mounts%20and%20enhancements/raspi/Pi_4_Case_40mm_fan_top%20v3.stl)
   * [pi 4 bottom](https://github.com/paenian/PrintShift/blob/main/prusa%20mini/mini%20mounts%20and%20enhancements/raspi/Pi_4_Case_bottom%20v3.stl)
   * [pi 3 top](https://github.com/paenian/PrintShift/blob/main/prusa%20mini/mini%20mounts%20and%20enhancements/raspi/pi_3_case_top.stl)
   * [pi 3 bottom](https://github.com/paenian/PrintShift/blob/main/prusa%20mini/mini%20mounts%20and%20enhancements/raspi/pi_3_case_bottom.stl)
3. Camera Mount
   * [pi rear center camera mount](https://github.com/paenian/PrintShift/blob/main/prusa%20mini/mini%20mounts%20and%20enhancements/raspi/pi%20camera%20mount%20-%20rear.stl)
   * [front corner webcam mount](https://github.com/paenian/PrintShift/blob/main/prusa%20mini/mini%20mounts%20and%20enhancements/raspi/corner%20webcam%20mount.stl)
     * The webcam mount I made has a 1/4" hole - common mounting for webcams in the US is 1/4x20 bolt
4. 4 * M2.5 screws, 35mm long.  These go through the mounting points, through the case top and bottom, AND through the Pi.  You could get away with long M3 screws, but you'd have to drill out all those components.
5. 4 * M2.5 hex nuts
6. Raspberry Pi 3 or 4 - either's fine, don't need extra ram or anything.  I don't run active cooling on my octoprint pi's, but certainly feel free to throw a fan on.
7. Pi Camera, OR webcam - see octoprint.org for compatible, but most will work.
   * With a Pi Camera, I also get a longer cable - something like 200mm - so that you can attach it to the bed.  A fixed camera is pretty rough when printing, attaching the camera to the bed works a lot better.

## Tools Needed
 * 2mm hex key
 * needlenose pliers

## Steps
1. Download and install Octopi onto a handy microSD card.
   * The [Octopi Instructions](https://octoprint.org/download/) are amazing and I'm not gonna repeat 'em here.
   * Put the card into your Raspberry Pi - it's possible to do (and remove) after installation, but it's more finicky.
2. Install the Raspberry Pi
   * You'll need all of the 2.5mm screws and nuts, and the pi camera cable if you're going that route.  (Webcams can be plugged in later)
   * If you have a heatsink or fan for your Pi, now's the time to install it.
     * I've never had heat issues, but usually use a passive heatsink if I can find one lying around
   * Install the pi camera ribbon cable onto the Pi, and feed it out of the pi case top.
   * The pi should follow, into the top of the case - then the bottom, of course.
   * Install the pi in its case so that the power plug is facing out, and the ports are facing towards the Prusa Mini's power.
     * it's cool to put a pi in upside down.  All the kids are doing it.
   * You should be able to plug in the power from your buck converter installed when wiring up the motor - now's a good time to make sure it'll reach :-)
3. Install your pi camera using the cable that should be sticking out, OR your webcam.
4. Fire it up!
5. Install Plugins
   * [Continuous Print](https://plugins.octoprint.org/plugins/continuousprint/) - Nice local plugin for repeat-printing.  By default it has a bed clearing script - you can either put the start/end gcode in there, or make it blank and keep the gcode files with ejection code.  For portability, I prefer to keep each file having its own bed clearing - that way I can use other print services.
6. Explore Cloud Printing!
   * [Autodrop3d](https://www.autodrop3d.com/)
   * [Polar Cloud](https://about.polar3d.com/octoprint)
   * [Raise3d Cloud](https://cloud.raise3d.com/raise3d.html)
   * [Spaghetti Detective](https://www.thespaghettidetective.com/)

## Congratulations!
With this step, you've got a fully functional part-ejecting 3D Printer that can be controlled from anywhere in the world -

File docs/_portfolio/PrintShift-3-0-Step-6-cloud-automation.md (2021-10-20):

---
title: "PrintShift 3.0 Step 6: Cloud Installation"
---

# PrintShift 3.0 Build Series: Step 6

This step is about adding plugins to Octoprint in order to enable cloud printing.  It will be continually updated

### Previous Step:
[PrintShift Step 5: Unleash Octoprint!](/portfolio/PrintShift-3-0-Step-5-pi-and-octopi-install)
### Next Step:
[PrintShift Step 6: Too Much Automation](/portfolio/PrintShift-3-0-Step-6-cloud-automation)

## Materials Needed
1. Prusa Mini, assembled, printing, with the conveyor belt bed, ejector motor, controls, and the Raspberry Pi attached and loaded up with Octoprint.  Yeah.
2. Electrons

## Tools Needed
 * A computer to pester your Octoprint install with

## Cloud Options
1. Autodrop 3d
2. Spaghetti Detective
3. Raise3d Cloud
4. add more :-)

## Cloud Services
One way to get more out of your part-ejecting 3D Printer is to put it on the CLOUD.  The benefit of a cloud service is that it puts your 3D Printer online, so that you can monitor it remotely and even start prints.  There are, of course, other ways to do this like tunneling through your router, but the cloud takes care of security and configuration headaches.

## Congratulations!
With this step, you've got a fully functional part-ejecting 3D Printer that can be controlled from anywhere in the world - and by anyone if you're not careful!  Happy printing, as always.

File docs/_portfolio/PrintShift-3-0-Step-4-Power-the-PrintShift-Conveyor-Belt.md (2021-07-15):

---
title: "PrintShift 3.0 Step 4: Power the PrintShift Conveyor Belt"
---

# PrintShift 3.0 Build Series: Step 4

This chapter includes both how to power AND how to control your PrintShift ejector!  For this build, the control system is moving the Z axis to the top and activating a microswitch to turn on the ejector motor.

I'll post an alternative control later - using a relay activated by the raspberry pi.

### Previous Step:
[Motorize the PrintShift Conveyor Belt](/portfolio/PrintShift-3-0-Step-3-Motorize-the-PrintShift-Conveyor-Belt)
### Next Step:
[PrintShift Gcode: Ejecting Parts](/portfolio/PrintShift-3-0-Step-4.5-PrintShift-Gcode)

## Materials Needed
1. Prusa Mini, assembled, printing, with the conveyor belt bed and ejector motor already attached.
  * see [PrintShift Step 3](/portfolio//portfolio/PrintShift-3-0-Step-3-Motorize-the-PrintShift-Conveyor-Belt) for details.
2. Parts Printed in Step 1, from the [Small Parts](https://github.com/paenian/PrintShift/blob/main/prusa%20mini/printshift%203.0%20ejector/PrintShift%20-%20all%20small%20parts.stl) stl
  * 1 - [limit switch mount](https://github.com/paenian/PrintShift/blob/main/prusa%20mini/printshift%203.0%20ejector/limit%20switch%20mount.stl)
3. Parts from the [Parts Kit](/portfolio/Bill-of-Materials)
  *  3 - M3 screw, 12mm long
  *  3 - post-instert 3030 T-Nut, m3 tapped
  *  1 - ring terminal
  *  1 - microswitch
  *  various lengths of wire
  *  3 - wire nuts
  *  1 - 24v->5v buck converter (optional, only needed if you want to add a pi later (hint: you do))
  *  4 - heat shrink solder tubes
  *  4 - zip ties

## Tools Needed
1. 2.5mm allen key
2. wire cutter/stripper
3. heat gun

## Procedure
1. First the microswitch, since we need to wire it up before installing.
   * There are three pins on the microswitch
     * C - Common, at the root of the lever
     * NO - Normally Open, in the middle
     * NC - Normally Closed, at the roller or end of the lever
   * We're going to connect C and NO; that means that, normally the switch is off, but when we press the lever it will turn the motor on.
   * First cut 2 of the heat shrink solder tubes so that there's only a little heatshrink past the solder
   * then thread both onto the same (at least) 40" or 1 meter length of red wire, long sides together.
     * Later we'll cut this wire - one side goes to the motor, the other goes to the HOT junction
     * for now, though, it's easier to leave it long
   * Strip the ends of the wire, and thread one end through the C terminal, and the other through the NO terminal
   * Slide the heat shrink solder tubes into place, and heat til the solder melts onto the wire + terminal
2. The microswitch then gets mounted to the top front of the Z axis
   * Insert the loop of wire first, and then the microswitch into the microswitch mount.  The lever end should point AWAY from the mounting hole!
     * Use a small zip tie to secure the microswitch
   * Take one 12mm M3 screw and one post-insert T-Nut and mount the [limit switch mount](https://github.com/paenian/PrintShift/blob/main/prusa%20mini/printshift%203.0%20ejector/limit%20switch%20mount.stl) to the front, top of the Z axis
   * The bottom of the microswitch mount's should be just above the top of the Z axis extrusion - but we can fine-adjust it later.
3. Mount the buck converter
   * Using two 12mm M3 screws and two post-insert T-Nuts, mount the microswitch on the bottom of the right side of the Z extrusion
     * Make sure the wires are facing the rear - it looks nicer.
4. Wire up the Motor
   * Run the wire from the microswitch (still un cut) over to the motor.  I like to zip tie it to the Y motor cable to help keep it out of the way.
   * We're going to connect it to the + terminal on the motor
   * Cut the wire a bit longer than you need to reach the motor and strip the end
   * Thread the wire onto the motor's + terminal, and using another heat shrink solder tube melt it into place.
   * Get your other wire, and similarly attach one end of it to the motor.
   * You can run it back parallel to the red wire
5. Next we're going to wire up the microswitch
   * Power from the mini goes into a wire nut, and from there goes to the microswitch and the buck converter
   * Neutral from the mini goes into a wire nut, and from there goes to the motor and the buck converter
     * If you wired the motor backwards, you can switch the motor and the microswitch to the opposite wire nuts :-)
   * The wire nuts can slot right into the 3030 extrusion and provide good wire management
   * So cut off some of the non-motor red wire from the microswitch (again leaving a bit extra) such that it'll reach the bottom of the Z extrusion.
     * Strip all three ends
     * In the wire nut, put the red microswitch wire, the red buck converter wire, and one end of the red wire you just cut off
     * You might need to strip the buck converter wire to get a good connection
     * Just leave the end for now
6. Next, wire up the buck converter
   * The converter got half-wired in the previous step
   * Cut the end off of the not-red wire from the motor such that it easily reaches the bottom of the Z extrusion
     * Strip all three ends again
     * In the wire nut, put the not-red motor wire, the black buck converter wire, and one end of the not-red wire you just cut off
7. CHECK your wiring!
   * You should have two stripped, unconnected wire ends - red and not-red - and no other unconnected wire.
   * Red goes to a wire nut, which then goes to the buck converter and the the microswitch.
     * The microswitch has one wire coming in from the wire nut, and one running over to the motor.
   * Not-red goes to a wire nut, then to the buck converter and then to the motor.
8. UNPLUG the Prusa Mini!!!
   * I mean, it should've been unplugged this whole time...
9. Open up the electronics case
   * The RED wire is powered from the power switch - either the always-on leg, or the switched leg.
     * Either way is fine - mainly depends on if you want the Pi on when the printer is off.
     * Slide one of the switch connectors off, put the stripped red wire through the hole in the terminal, and slide the connector back on
   * The other wire needs a ring terminal crimped onto it - this can be done with pliers, but most wire strippers will have a pokey crimp lug.
     * Once the wire is crimped, we need a 2.5mm hex driver to remove one of the Buddy Boards screws - right by the power inlet.
     * The screw goes through the ring terminal and right back - it's connected to the ground plane of the buddy board.
10. DONE!  I know it's a lot of fiddling, but the wiring's not too bad.
     
## Video Walkthrough
{% include video id="kofxEpY8BTg" provider="youtube" %}

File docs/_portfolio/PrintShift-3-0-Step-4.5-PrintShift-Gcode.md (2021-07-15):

---
title: "PrintShift 3.0 Step 4.5: PrintShift Gcode: Ejecting Parts"
---

# PrintShift 3.0 Build Series: Step 5

This is a short, non-building section to discuss PrintShift Gcode.  It's not truly a step, and will hopefully serve as a reference in the future.  If you're in a hurry, no worries - all you NEED to do is copy in the start and end gcode.  I've annotated the gcode itself, so hopefully it's easy enough to edit later, or adapt to your non-Prusa Mini or your non-Prusa slicer.

### Previous Step:
[Power the PrintShift Belt](/portfolio/PrintShift-3-0-Step-4-Power-the-PrintShift-Conveyor-Belt)
### Next Step:
[Installing Octoprint](/portfolio/PrintShift-3-0-Step-5-PrintShift-Gcode)

## Materials Needed
1. Prusa Mini, assembled, printing, with the conveyor belt bed, ejector motor, and control microswitch attached and wired together.

## Tools Needed
1. Computer of some description
2. PrusaSlicer, or your slicer of choice

## Start & End Gcode
[Latest Github Start and End Gcode](https://github.com/paenian/PrintShift/blob/main/prusa%20mini/PrusaSlicer%20Profile/start_and_end_gcode.txt)

 * The Start Gcode heats up the bed, gives it a spin to even out the heating (I call it the barbecue roll), and then proceeds with the usual Prusa routine of leveling, purging (new purge location, so that it ends up on the belt), heating and printing.
 * The End Gcode cools the printer, parks the extruder, and then runs the bed ejection.  The pause is simply a timed pause; an easy modification is to have the printer wait until the bed cools to a certain temperature, but that's not ideal for me because I switch between PLA and PETG often.  Waiting for PETG to cool off to PETG ejector temps takes a while, and ejecting PLA at PETG bed temps gives you mildly rolled parts!  So yeah.  Timed Pause.  Not exciting, but it works well.

## Full PrusaSlicer Profile
[Latest Github PrusaSlicer Profile](https://github.com/paenian/PrintShift/blob/main/prusa%20mini/PrusaSlicer%20Profile/PrusaSlicer_PrintShift_Config.ini)

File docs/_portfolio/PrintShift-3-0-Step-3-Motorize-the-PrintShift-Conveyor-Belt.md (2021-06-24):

---
title: "PrintShift 3.0 Step 3: Motorize the PrintShift Conveyor Belt"
---

# PrintShift 3.0 Build Series: Step 3

This page details how to install the motor which drives PrintShift conveyor belt that we built in step 2.  This is just the mechanical build - the electrical wiring and control are in step 4. At the end of this step, the motor will be mounted and linked to the conveyor belt.

### Previous Step:
[PrintShift Belted Bed Build](/portfolio/PrintShift-3-0-Step-2-Belted-Bed-Build)
### Next Step:
[Power the PrintShift Belt](/portfolio/PrintShift-3-0-Step-4-Power-the-PrintShift-Conveyor-Belt)

## Materials Needed
1. Prusa Mini, assembled, printing, with the conveyor belt bed attached.
  * see [PrintShift Step 2](/portfolio/PrintShift-3-0-Step-2-Belted-Bed-Build) for details.
2. Parts Printed in Step 1, from the [Small Parts](https://github.com/paenian/PrintShift/blob/main/prusa%20mini/printshift%203.0%20ejector/PrintShift%20-%20all%20small%20parts.stl) stl
  * 1 - [mini cable cover](https://github.com/paenian/PrintShift/blob/main/prusa%20mini/printshift%203.0%20ejector/MINI-heatbed-cable-cover-bottom.stl)
  * 2 - (one mirrored) - [fixed bushing](https://github.com/paenian/PrintShift/blob/main/prusa%20mini/printshift%203.0%20ejector/lifted%20belt%20shaft%20mount%20-%20fixed%20bushing.stl)
3. Parts from the [Parts Kit](/portfolio/Bill-of-Materials)
  *  1 - 8mm shaft collar
  *  1 - 8mm shaft, 210mm long

## Tools Needed
1. 2.5mm allen key - for the headbed cable cover replacement
2. 2mm allen key - for our new bed screws
3. needlenose pliers

## Procedure
1. 

## Video Walkthrough
{% include video id="kofxEpY8BTg" provider="youtube" %}

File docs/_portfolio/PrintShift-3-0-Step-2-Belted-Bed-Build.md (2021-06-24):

---
title: "PrintShift 3.0 Step 2: Belted Bed Build"
---

# PrintShift 3.0 Build Series: Step 2

This page details how to assemble the PrintShift bed with its conveyor belt, rollers and tensioners.  At the end of this step, you will be able to run test prints on your bed material, but the ejector will not be assembled.

### Previous Step:
[Printing PrintShift Parts on your Prusa Mini](/portfolio/PrintShift-3-0-Step-1-Printing-PrintShift-Parts-on-your-Prusa-Mini)
[Building-a-Continuous-Belt](/portfolio/Building-a-Continuous-Belt/)

### Next Step:
[Powering the PrintShift Conveyor Belt](/portfolio/PrintShift-3-0-Step-3-Motorize-the-PrintShift-Conveyor-Belt)

## Materials Needed
1. Prusa Mini, assembled and printing, preferably having just printed the parts you'll need for this step :-)
  * see [PrintShift Step 1](/portfolio/PrintShift-3-0-Step-1-Printing-PrintShift-Parts-on-your-Prusa-Mini) for details.
2. Parts Printed in Step 1, from the [Small Parts](https://github.com/paenian/PrintShift/blob/main/prusa%20mini/printshift%203.0%20ejector/PrintShift%20-%20all%20small%20parts.stl) stl
  * 1 - [mini cable cover](https://github.com/paenian/PrintShift/blob/main/prusa%20mini/printshift%203.0%20ejector/MINI-heatbed-cable-cover-bottom.stl)
  * 2 - (one mirrored) - [fixed bushing](https://github.com/paenian/PrintShift/blob/main/prusa%20mini/printshift%203.0%20ejector/lifted%20belt%20shaft%20mount%20-%20fixed%20bushing.stl)
  * 2 - (one mirrored) - [tensioner rod holder]https://github.com/paenian/PrintShift/blob/main/prusa%20mini/printshift%203.0%20ejector/lifted%20tensioner%20rod%20holder.stl)
  * 2 - (one mirrored) - [tensioner body](https://github.com/paenian/PrintShift/blob/main/prusa%20mini/printshift%203.0%20ejector/tensioner%20body.stl)
3. Parts from the [Parts Kit](/portfolio/Bill-of-Materials)
  *  1 - 8mm shaft collar
  *  1 - 8mm shaft, 210mm long
  *  1 - 8mm shaft, 183mm long
  *  2 - 8mm flanged bushing
  *  6 - m3 hex standoffs, 10mm long
  *  6 - m3 flathead screws, 8mm long
  *  2 - m5 screws, 25mm long
  *  2 - m5 hex nuts, thin
  *  1 - EPDM foam tube
4. A continuous conveyor belt loop - 435mm long, 155mm wide:
  * [Building-a-Continuous-Belt](/portfolio/Building-a-Continuous-Belt/)

## Tools Needed
1. 2.5mm allen key - for the headbed cable cover replacement
2. 2mm allen key - for our new bed screws
3. needlenose pliers
4. TX10 Torx key - for Prusa's bed screws

## Procedure
1. Remove the Prusa Mini bed and the old standoffs
   * Set aside the spring steel print surface
   * Use your TX10 Torx wrench to remove the Prusa Mini's bed.  We're not re-using these screws.
   * Use pliers or a 5mm hex socket to remove the center row of standoffs - they get in the way of the belt.  These will not be reused either.
   * The 
2. Replace the heated bed cable cover to make room for the belt tensioner mount
   * 2.5mm allen key to remove the screw - keep it handy, we use the same screw
   * Slide the cable cover out
   * Move the 3mm locknut to your new cable cover
   * screw in the new cover with the old screw.
3. Replace the six remaining standoffs - going from the original 6mm to fancy new 10mm
   * I put the mini at the edge of a table, and slide the belt all the way forward to replace the front six
   * Rotate, slide the bed all the way back to replace the rear six
   * Re-use the original Prusa Mini screws, but you do not need the 6mm standoffs again.
   * Be sure to tighten the standoffs on, and optionally use some loctite - these will remain in place while we unscrew the bed to swap belts.
4. Build and add the drive rail.
   * The longer drive rail needs to have its shaft coller screwed to one end.
   * Then, insert the brass bushings into the [fixed bushing](https://github.com/paenian/PrintShift/blob/main/prusa%20mini/printshift%203.0%20ejector/lifted%20belt%20shaft%20mount%20-%20fixed%20bushing.stl)
     * There's an indent for the bushing's flange on the printed fixed bushing - be sure it's on correctly!
   * Slide the drive shaft through the front bushing
   * Slide the EPDM foam onto the roller - a little air from the open side helps a LOT.
   * Slide the rear bushing on, and then place the drive roller onto the left-side standoffs.
   * Finally, you can clamp one one side of the shaft coupler to complete the mount.
5. Assemble the Tensioner Mounts!
   * Snap an M5 nut into the [tensioner body](https://github.com/paenian/PrintShift/blob/main/prusa%20mini/printshift%203.0%20ejector/tensioner%20body.stl)
     * times two!
   * Screw your 25mm M5 screw into the tensioner body through the nut
   * Insert the [tensioner rod holder](https://github.com/paenian/PrintShift/blob/main/prusa%20mini/printshift%203.0%20ejector/lifted%20tensioner%20rod%20holder.stl) into the body
   * Insert the idler rod into either side of the tensioner rod holders
   * The tensioner body, as well as the rod holder can then be positioned on the right-side hex standoffs.
6. Mount the Belt - you're almost done!  This is the same procedure as changing the belt
   * First, de-tension the idler as much as you can, sliding the idler in towards the center of the bed
   * Loosely screw the back three screws for the heated bed in place - using our new, 8mm M3 flat-head screws
   * Lift the front of the bed, and remove the front side of the tensioner and idler rods, angling them in towards the center of the bed
   * This will let you slide the belt on, all the way til it's touching the rear center hex standoff
   * Put the drive and idler rod holders back on their hex standoffs, and close up the bed
   * Tighten all six front and rear bed screws
   * With the belt still untensioned, slide the spring steel print surface in between the heated bed and the belt
   * Tension the bed

At this point, you can start a test print!  It won't eject yet, unless you manually rotate the shaft coupler.

## Video Walkthrough
{% include video id="plg7Tx-Cm6E" provider="youtube" %}

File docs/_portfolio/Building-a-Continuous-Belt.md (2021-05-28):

---
title: "Making a Continuous Belt from sheet stock"
---

# Making a Continuous Belt.

This page details how to build a continuous loop conveyor belt from a flat sheet of material.   It will enable you to test out any material on your PrintShift or other belt-based printer, and is widely applicable for joining strips of material.  

## Materials Needed
1. Belt Joining Tape.  What sort of tape!?  Three things to consider are:
   * Tape Material
   * Tape Thickness
   * Tape Adhesive
2. Belt.  Again, what sort?
   * You need a strip ~20mm longer than your final loop size, cut to the correct width.
3. Painter's Tape
   * This is used to hold the belt in place while assembling, and discarded afterwards.  1" wide is fine; pictured below use 2" wide.

## Tools Needed
1. Block of wood to cut on.
   * If your printer can't slide a continuous belt on, a thin piece of HDPE or similar (cutting mat) is recommended to protect your bed.
2. Sharp knife capable of cutting your belt.
3. Light.  Do not attempt in darkness.

## Procedure
1. Place belt outside-down on your work surface.
2. Place block of wood on top.
3. Form the belt into an overlapping loop - lining up the straightest edge with itself.
4. Tape the belt into a loop
5. Thoroughly tape the belt to the wood cutting block on either side of the joining tape line.
6. Cut through BOTH layers of the belt.
   * cutting at a slight angle will help maintain belt tension over the seam.
7. Remove the ends of the belt carefully - the goal is not to disturb the joint.
8. Join the belt ends with your Belt Joining Tape.
9. Woo it's a belt!  Carefully remove the blue tape and install it on your printer.

## Video Walkthrough
{% include video id="_wT68gNBn74" provider="youtube" %}

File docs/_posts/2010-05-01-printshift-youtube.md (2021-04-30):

---
title: "PrintShift on YouTube!"
categories:
  - Blog
tags:
  - link
  - Post Formats
link: https://youtube.com/paulchase
---

There is a nice pile of PrintShift videos already up on YouTube!  Check 'em out.

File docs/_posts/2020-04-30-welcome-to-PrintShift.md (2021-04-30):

---
title: "Welcome to PrintShift!"
date: 2020-04-30T15:34:30-04:00
categories:
  - blog
  - PrintShift
tags:
  - update
---

This is the official landing page for the PrintShift project.

The PrintShift Project is adding conveyor belts to conventional 3D printers.  The project began by adding part ejection to Prusa Minis, which is now feature-complete and has been running for thousands of printing hours.

The project will continue to work on belts, part ejection and related technologies, as well as working to improve the Prusa Mini's ejector.

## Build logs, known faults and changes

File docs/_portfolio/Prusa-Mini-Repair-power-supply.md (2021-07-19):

---
title: "Prusa Mini Repair: Mini Power Supply"
---

So, let's say your Prusa Mini power supply kicks the bucket.  Can you fix it?  Should you fix it?  In this video I'll show you how to diagnose power problems on a Prusa Mini, and take a look inside the supply to see if there's any user-fixable parts in that.

## Testing the Supply
If you suspect that your mini's power supply is damaged, the best way to test is to use a multimeter to see if it's producing 24 volts.  The mini uses a round four pin plug.  Two of the pins are for power input, the other two are ground - and the sheath is theoretically a separate ground, but they are all tied together on the Buddy Board.  Testing this supply at the plug is somewhat problematic - because your two power pins are surrounded by ground pins, and it's very easy to short power to ground with your typical multimeter probe.

Instead I recommend testing on the mini itself by removing the electronics cover.  This exposes some easy probe points, and will also let you check the mini's fuses.  If your mini won't power on at all, there are a few things to test: power coming in, power making it past the power switch, and the fuses.

### Power Coming In
First off, all grounded points on the buddy board are tied together - so to test power in, any of the mounting screws will work great.  For 24v, the pad closest to the plug is the power's first destination, going into a faston connector over to the power switch.

### Power Switch
After that, power goes to the power switch, and if that's turned on right back to the next faston connector.

### Fuses
With the switch on, we can test the fuses.  There are two - one for the heated bed that's a [7.5 amp fuse](https://www.digikey.com/en/products/detail/littelfuse-inc/0297010-WXNV/146591) and one for everything else, a [3 amp fuse](https://www.digikey.com/en/products/detail/littelfuse-inc/0297003-U/3427703).  These are standard car fuses, available pretty much any auto place, and you can visibly see the fusible link - that wire in the middle - if the fuse is blown it's because that wire vaporized.

If you're not great with numbers, or, um, reading, you can see that the [7.5 amp fuse](https://www.digikey.com/en/products/detail/littelfuse-inc/0297010-WXNV/146591) has a much thicker wire than the [3 amp fuse](https://www.digikey.com/en/products/detail/littelfuse-inc/0297003-U/3427703).  The whole idea being that, if the current going in is too high, the fuse will die before any of your expensive, difficult to replace electronic componenets.

A quick side note.  If you do blow a fuse... what happened?  Why did the fuse blow?  If you don't know what caused the excessive power draw, replacing the fuse might not fix the problem.  Certainly could be a power surge, or a voltage issue - but anytime you see a blown fuse, take a look around before you jam a penny in its place.

### Replacement
Switches and fuses are easy enough to replace; links to parts down in the description.  In a pinch you can bypass the switch and just jumper from one faston to the other, no problem.  Bypassing the fuse, or running the wrong rating will work, too, but you risk catastrophic damage to your buddy board.  Fuses are cheap - get the right one.

If your supply's been hit by a tiny meteorite or otherwise beyond repair, replacements are available from [Prusa Research](https://shop.prusa3d.com/en/minimini/1026-psu.html), but they're pretty expensive.

The connector is a 4-pin Mini-Din Kycon Snap and Lock DC Power Connector.  You can replace the connector alone, if say it's bent or something, or even buy a replacement to add on to another 24v supply you have lying around.

If you need to replace the connector, [digikey](https://www.digikey.at/product-detail/en/kycon-inc/KPPX-4P/2092-KPPX-4P-ND/9990085?cur=EUR&lang=en) sells them, and has links to the datasheet so you can find the connector on your preferred electronics site.

You could also easily bypass the connector, and run 24v right into the buddy board; for this, I would use a ring terminal for the ground and connect the power wire directly to the power switch... like I do to power my PrintShift part ejection system.  This isn't a shameless plug, mind.  I am mildly ashamed.

## What's inside?
If your power supply has failed, are there any user servicable parts inside?  Hope so.  I'll be opening it to see what's in there.  I'm not an electrical engineer, my background is computer science but I've been around power supplies for some time.  Mostly, you look for the part that's burnt and replace it.

Upon opening, the supply is wrapped in an aluminum shield and heat spreader, that appears to be spot-welded on.  There is a soldered-in fuse on the AC side, however - a 5 amp 250v slow-blow fuse.  [T5A 5A 250V Fuse](https://www.walmart.com/ip/10Pcs-DIP-Mounted-Square-Slow-Blow-Micro-Fuse-T5A-5A-250V-Black/678411349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)

{% capture fig_img %}
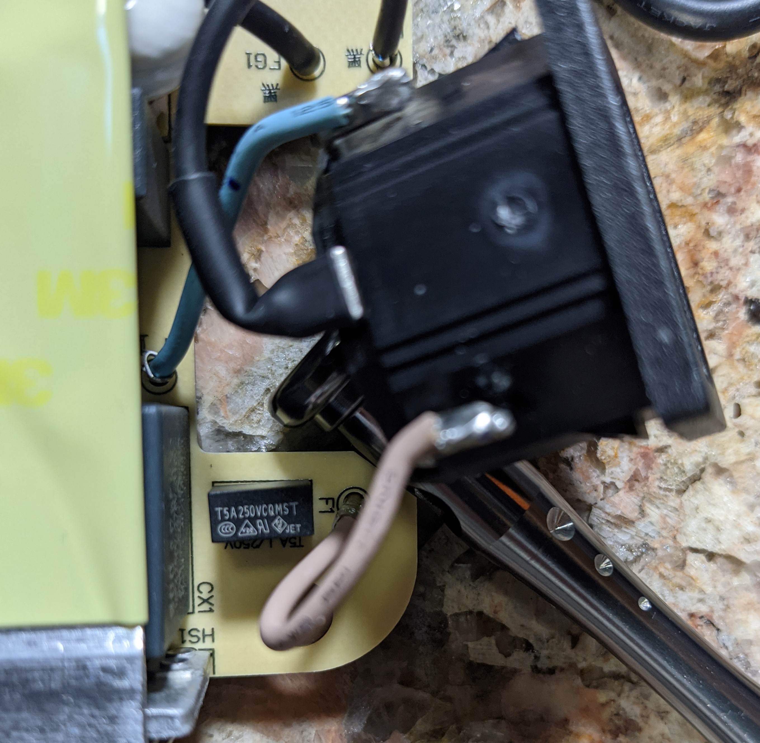
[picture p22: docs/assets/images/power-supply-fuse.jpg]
Fuse

{% endcapture %}

<figure>
  {{ fig_img | markdownify | remove: "<p>" | remove: "</p>" }}
  <figcaption>Picture of the fuse as it's installed.</figcaption>
</figure>

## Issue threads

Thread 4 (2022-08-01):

Aliex Motor does not fit

Bjerg, 2022-08-01:
im having trouble fitting this motor because it does not fit which i am aware of but i am unable to change the files because the step or f3d file is not available

this is the motor in question

https://www.aliexpress.com/item/32987942205.html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

would it be possible to get the step/f3d? or are you able to make a mount for it. i am more than happy to make it for you.

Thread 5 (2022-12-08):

about the Kapton film

hou130425, 2022-12-08:
Hello, I also tested the 0.2mm thick Kapton film. But I encountered a problem when printing the first layer, the print head is very close to the Kapton film, the Kapton will be deformed, and then recover, which causes the bottom of the print to become arc-shaped

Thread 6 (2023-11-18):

Prusa Mini + Print Shift 5.0: Why 155mm film?

dclaze, 2023-11-18:
I noticed in the BOM for Printshift 5.0 the required film width is 155mm, does this limit the printable surface area to 155 width?

Prusa Mini has a 180x180mm print surface so just curious if this is by design or if I should buy a wider film to get the full bed surface potential.

Reference: https://github.com/paenian/PrintShift/tree/main/prusa%20mini/printshift%205.0%20ejector

paenian, 2024-07-17:
The film is narrower than the bed, and limits the printable area that's ejectable.  The reason for that is so you can use the existing bed mounts - the belt is narrow to squeeze between them.

Closed 2024-07-17.

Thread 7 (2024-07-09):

Unable to find the tensioner for printshift v5

Bjerg, 2024-07-09:
i am unable to find the file for the tensioner for the belt? for the printshift v5 am i missing something?

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

paenian, 2024-07-17:
Here's the rod mount with the tensioner: https://github.com/paenian/PrintShift/blob/main/prusa%20mini/printshift%205.0%20ejector/tensioner%20rod%20mount%20right.stl

I just used 4 of them, two normal and two mirrored.  Add a 20mm M3 bolt and square M3 nut to tension the belt against the y-axis frame.

Closed 2024-07-17.

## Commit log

2021-04-30 Rename docs/_pages/PrintShift Instructions/Belt Materials.md to docs/_pages/PrintShift_Guides/Belt Materials.md
2021-04-30 Rename docs/_pages/PrintShift Instructions/Building-a-Continuous-Belt.md to docs/_pages/PrintShift_Guides/Building-a-Continuous-Belt.md
2021-04-30 Moved over MOST of the PrintShift STLs
    Working on the website
    [3030-dropin-tee-m3.stl, MINI-heatbed-cable-cover-bottom.stl, Pi_4_Case_40mm_fan_top v3.stl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]
2021-04-30 I believe this is all of the STLs loaded.
    [Orbiter-Mount-fan-spacer.stl, corner gopro mount.stl, giant clock mount.stl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]
2021-05-06 Adding a snapshot of the BOM
    Woo!
2021-05-06 Update and rename bazboomtest.md to Bill-of-Materials.md
2021-05-12 Updated BoM
    [PrintShift BOM - Sheet1.csv]
2021-05-20 Updated the tensioner body
    File was corrupted :-(
    [lifted tensioner rod holder.stl, tensioner body.stl]
2021-05-28 Instructions for Printing the PrintShift Parts!
    woo
2021-05-28 Adding the small parts
    [3030-dropin-tee-m3.stl, PrintShift - all small parts.stl, pi camera mount - rear.stl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]
2021-06-24 Adding an updated microswitch mount
    [limit switch mount.stl]
2021-07-08 Updating for smaller bushings, microswitch, etc
    [PrintShift - all small parts 10mm sleeve bushing.stl, PrintShift - all small parts 11mm bushing.stl, PrintShift - all small parts.stl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]
2021-07-15 Update and rename PrintShift-3-0-Step-6-pi-and-octopi-install.md to PrintShift-3-0-Step-5-pi-and-octopi-install.md
2021-07-15 Update and rename PrintShift-3-0-Step-5-PrintShift-Gcode.md to PrintShift-3-0-Step-4.5-PrintShift-Gcode.md
2021-07-23 Adding all the PrintShift logos
    [printshift.dxf]
2022-02-03 First commit of the Belt Deflection Tester
    Updated logos
    Created a new rear motor plate - this one matches the newest mini, but
    is unverified for now.
    [Belt Deflection Tester.stl, printshift_logo.dxf, rear motor plate updated.stl]
2022-02-03 Adding the large bed ejector as a sub-set
    Going to kill off the other project, having two was just confusing
    people.
    [100mm roller.stl, bed corner.stl, configuration.scad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]
2022-02-06 Bigified the belt tester, and beefed up my roller mounts
    MORE tension!
    [Belt Deflection Tester.stl, motor and drive roller mount.stl]
2022-06-03 Initial commit of PrintShift 4.0
    Goals of this release:
    1) stop stealing power from the printer - it gives users the heebie
    jeebies
    2) fewer parts! Easier install!
    Current status: testing.
    I'll get a readme/BOM up here as soon as it's semi working
    [Belt Deflection Tester.stl, MINI-heatbed-cable-cover-bottom.stl, Orbiter_2.0_Prusa_Mini.stl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]
2022-06-12 Updated the motor mount - printing now
    Should be good for install, but hasn't been tested yet.
    Still need to modify the tensioner rod holder, it doesn't retract in as
    much as it should.
    [direct mount motor lifted bushing.stl]
2022-06-13 Updated the tensioner, added belt jig
    [Prusa Mini Belt Jig.stl, tensioner rod holder bearing.stl]
2022-06-15 Added the belt jig source
    cuz I said I would in the video :-)
    [PrintShift Belt Jig v2.f3d]
2022-06-16 Adding the printed parts to the BOM.
    feedback helps make things clearer, hopefully!
2022-06-16 Added a plate of all the parts.
    [all parts arranged.stl]
2022-09-12 Adding an LM8UU mount for older minis
    [prusa mini lm8uu clamp.stl]
2023-09-25 First commit of PrintShift 5.
    Could use some refinement - but I like to keep things public.
    [left front rod mount.stl, ratchet.stl, sprag clutch ratchet wheel.stl]
2023-09-28 PrintShift 5.0 rotary rack and pinion
    Improved idea for actuating the bed roller - a rack that can be turned on and off via rotation. My first thought was to use a servo and a servo controller... but why not just use the Z axis and some 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
    So to advance the belt, you would:
    1. move printer to Max Z: this pulls a string that rotates the pinion such that the teeth are on top.
    2. Use the Y axis with its one-way-bearing endowed pinion to advance the bed as far as you want
    3. Drop the Z axis down so that a printed spring can return the rack to its disabled state.
    [correct spring.stl, rack mount.stl, rack.stl]
2023-10-27 Adding 5.1 parts
    [3030nutfoot_holed.stl, rack mount.stl, rack.stl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]
2024-07-17 Adding rod mount with tensioner
    For my builds, I printed four of these (well, two normal and two mirrored). They use an M3 square nut and M3x20mm screw to tension the rods.
    [tensioner rod mount right.stl]
